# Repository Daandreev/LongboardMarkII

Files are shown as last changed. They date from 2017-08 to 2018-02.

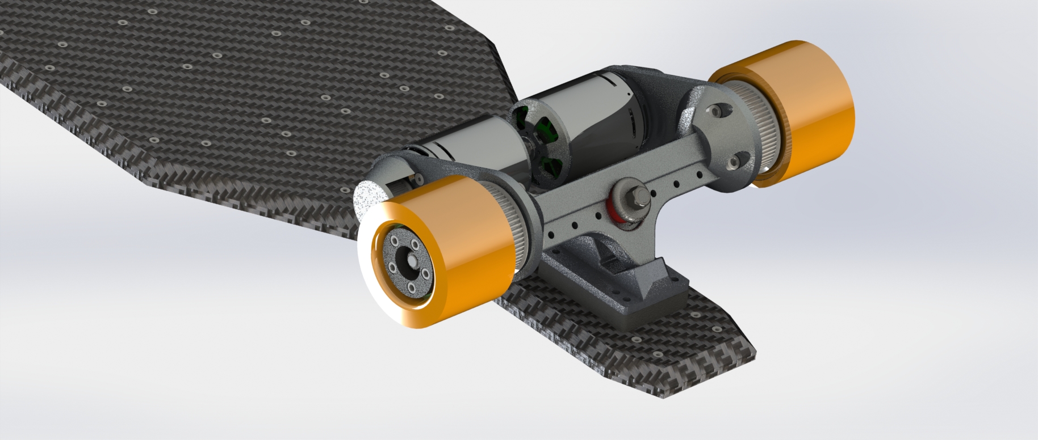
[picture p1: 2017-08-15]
CAD/MarkII/FullAssembly/Pictures/FullAssemblyImage1.JPG

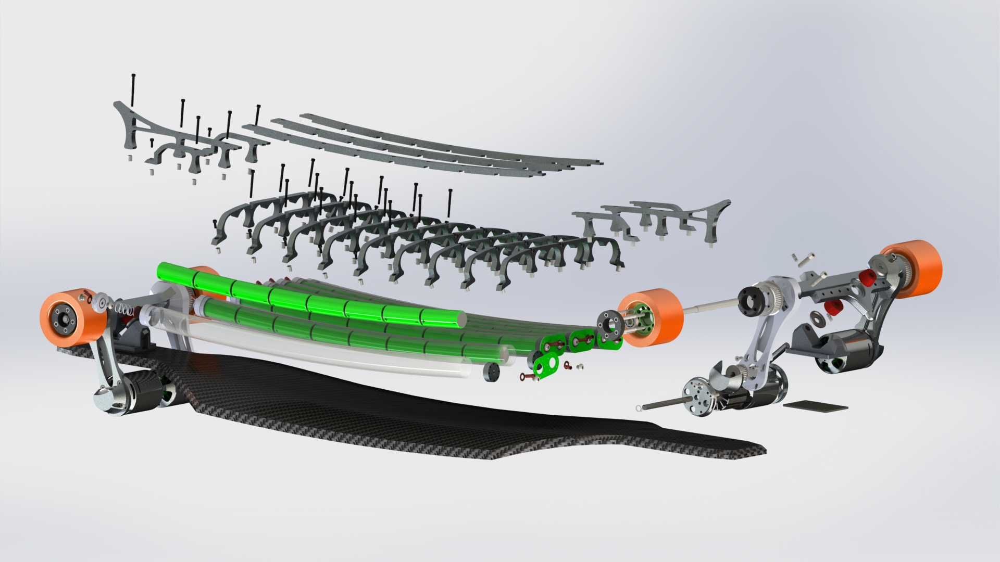
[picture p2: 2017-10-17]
Pictures/Full Assembly Exploded 2.JPG

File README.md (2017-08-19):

# LongboardMarkII

Ground up, over-engineered electric longboard

*****August 8, 2017*****

I want something under my ass that has enough potential energy packed into its batteries to fire a pound of bacon into the Asteroid Belt. 
Since nothing on the market fits the bill; I am building it myself.

With a sufficient disrespect for my own time and money I am learning every EE, ME, CS, Manufacturing technique necessary to complete aforementioned longboard.

The project started in my freshman year of college, Winter 2015.

[MarkI](https://www.instructables.com/id/Electric-Longboard-Mark-I/) was completed in the spring of 2016. It featured a whopping 35mph top speed, a pair of lead-acid scooter batteries giving it a theoretical range of about 4 miles of range, and a jaguaresque construction - requiring field-repairs every 2 miles.

MarkII was started soon after. Initially I focused on learning the electrical engineering skills necessary to create the Motor Drivers, BMS, and Headlights. 
	The Motor Drivers were my introduction to H-bridges and after creating a design that could vaguely spin a BLDC motor I opted out for [Vedder's VESC](http://vedder.se/2015/01/vesc-open-source-esc/)
	The BMS vas envisioned as an adaptive system that could be daisy chained across as many batteries as necessary, however that became more of a PCB design and manufacturing learning experience after I learned more about how they are made industrially.
	The headlights were and still are massively successful. With 5 watts of pure photon emission created by a triple bank of German OSRAM diodes, they are blindingly bright in all Red, Green, Blue and White colors. The issue is that I can’t run them on more than 10% brightness without facing serious heat management issues.
	
In parallel with the electronics, I created a few iterations of the deck. I constructed my own longboard-deck press by molding an initial foam model with cement. The initial few attempts at carbon fiber-foam composites failed, however on the 3rd iteration of the Baltic Birch - Carbon fiber Composite, I was able to produce a beautiful deck that stands at 48in tall and flexes less than an inch with 500lb on it.

I also learned how to use a few CAD packages, and CNC equipment to make the mounting hardware for the motors. Learning from the flimsy construction of the MarkI motor mounts I designed my own longboard trucks to accommodate the installation of a pair of 2250Watt motors. My designs were based on the Caliber II Longboard trucks.

As it stands, just about everything made in the past year needs to be reiterated.

My main focus now, is to involve more people. My friend Anton Zaytsev has been diligently helping me create a 1.5kW charger and another offered to do some of the software. However, I think this project can bring together a serious community interested in progressing high-tech DIY electrical vehicles.

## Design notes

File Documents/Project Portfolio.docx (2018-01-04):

Electric Longboard Mark II

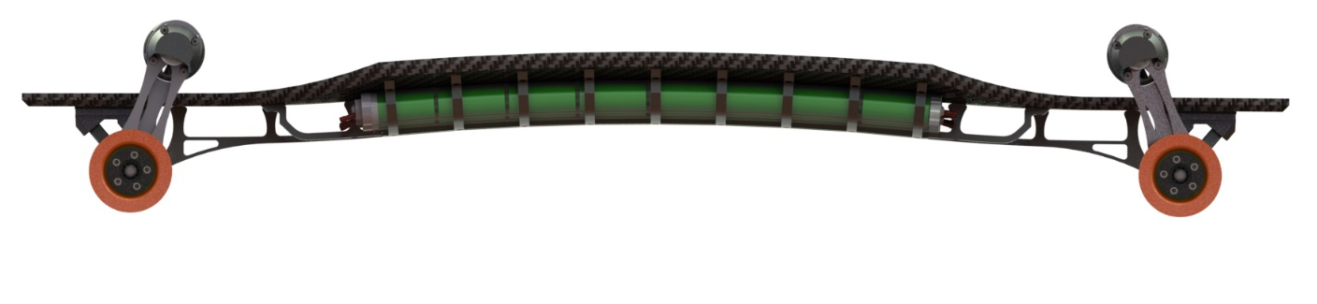
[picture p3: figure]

Open-Source Project by Daniil Andreev

Oct. 16, 2017

Motivation

The reasoning behind this project it is a natural progression of my interest in longboard and previous mechanics experience, as well as making a resume that I can literally ride to an interview. However, the initiating thought was; I want build something so outrageous it exists only in a Neal Stevenson universe.

The project started during the end of my first year as an undergrad at Knox College. I had looked at the commercially available Boosted Board and figured I could make something way more powerful.

Having no training in electronics, I spent the rest of the year attempting smaller projects that would help me build the skill required to attempt an electric vehicle. 3 years later I am just starting to see the finish line.

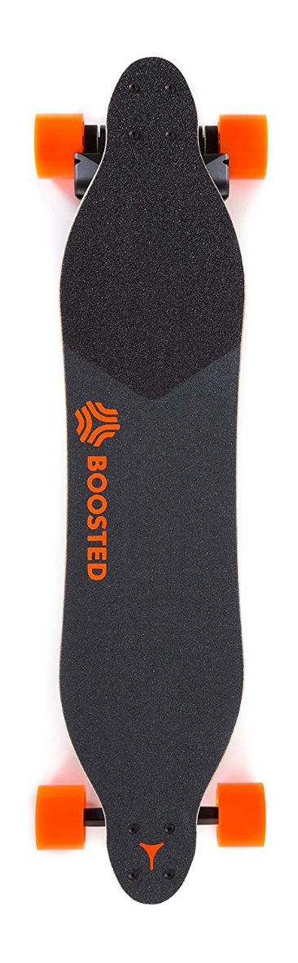
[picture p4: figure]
Image result for boosted
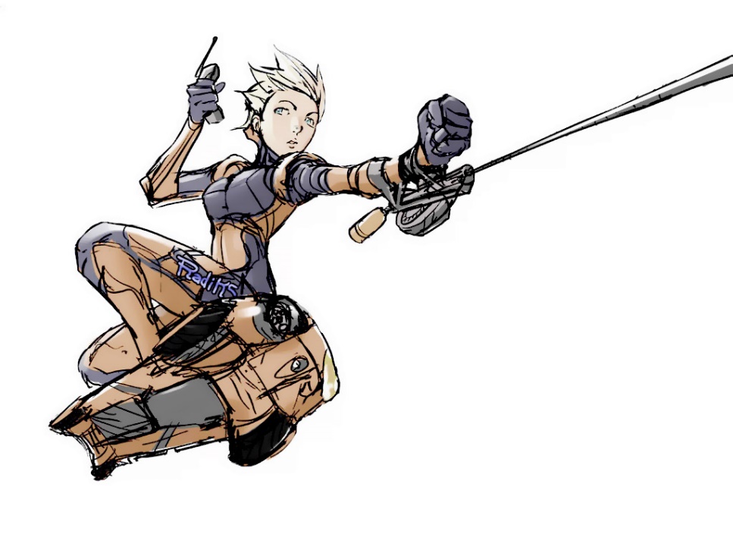
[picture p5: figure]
Image result for YT snow crash

Mechanical Design and Model

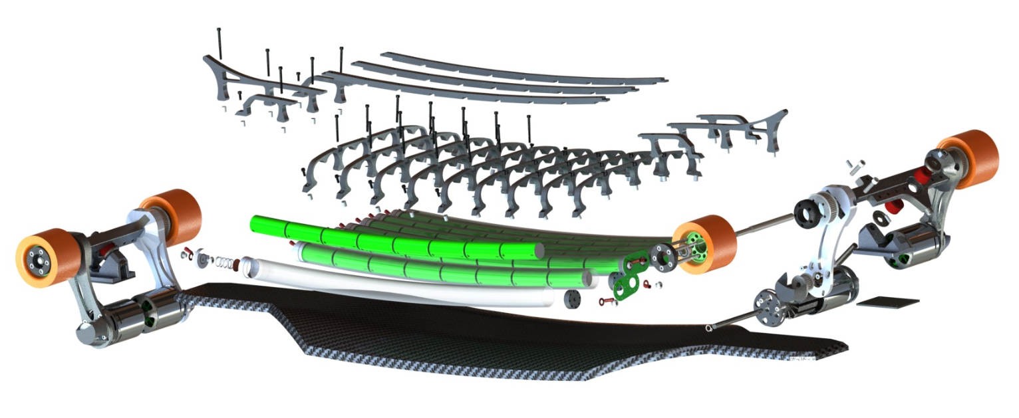
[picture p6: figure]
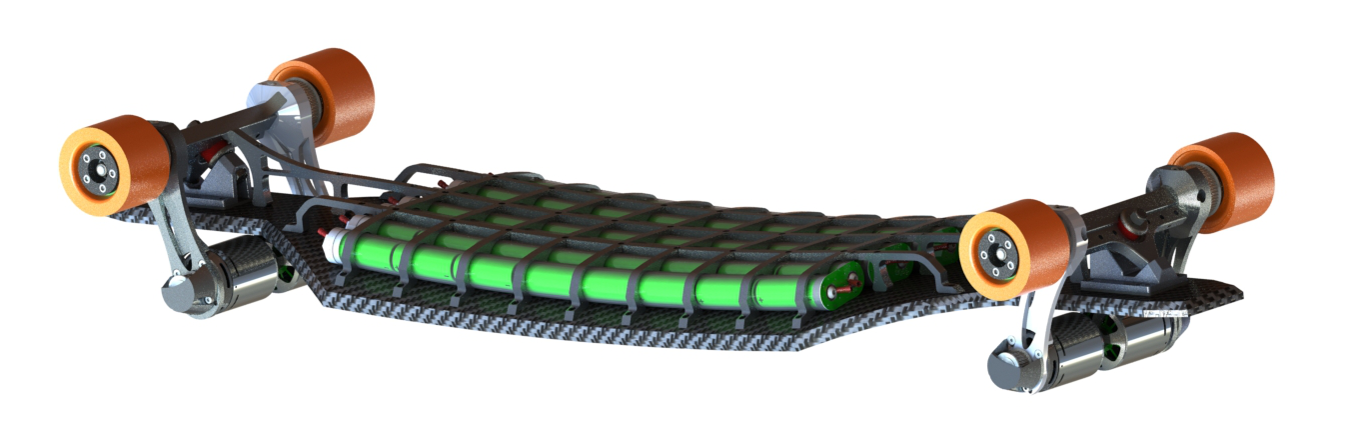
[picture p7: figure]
A close up of a device Description generated with very high confidence

After a year break in the building process I set out to reimagine the mechanical superstructure.

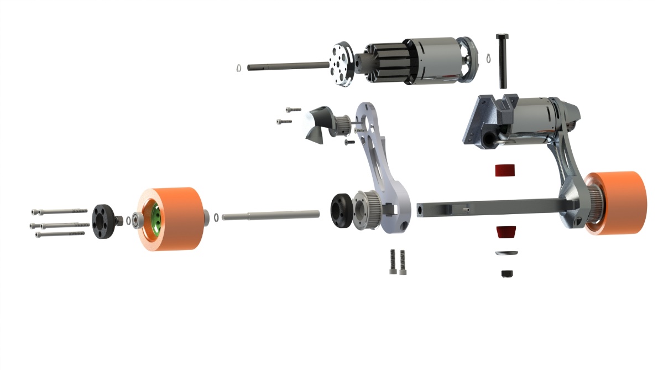
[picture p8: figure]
A close up of a device Description generated with high confidence

Completed

2015-2016

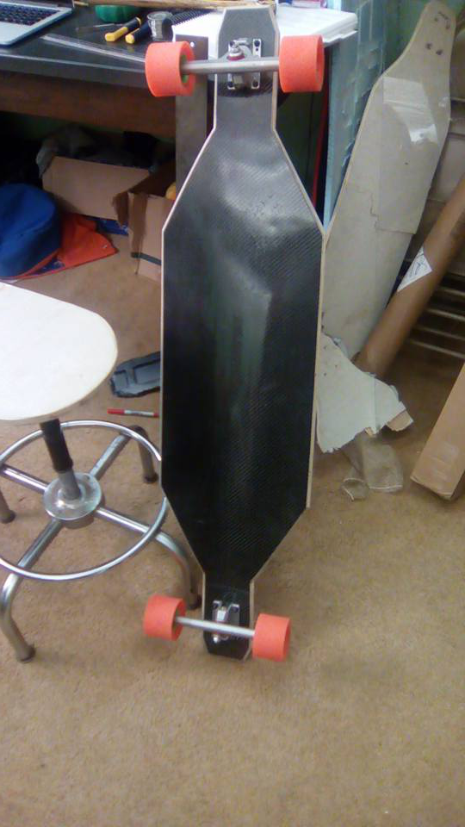
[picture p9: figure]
A picture containing indoor, floor, wall, table Description generated with very high confidence
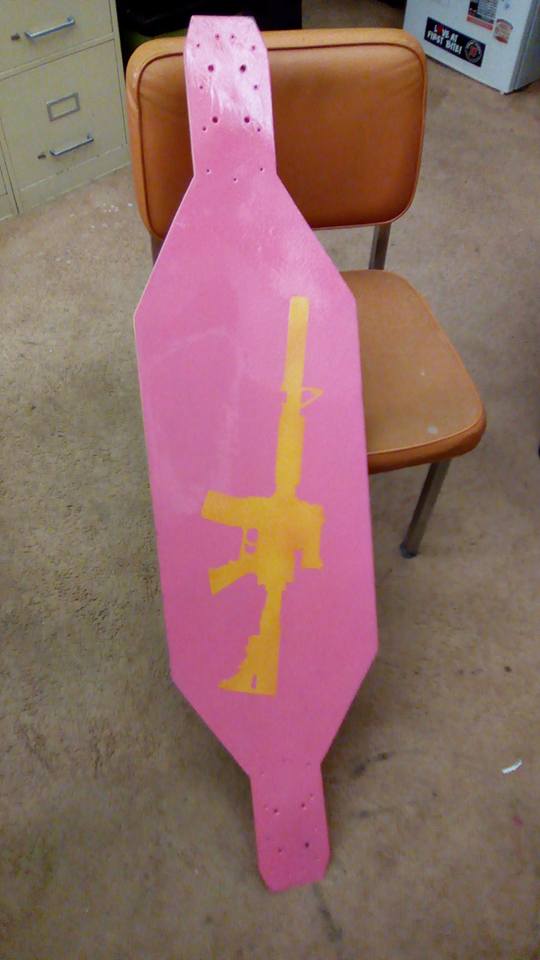
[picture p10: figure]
A sign on the floor Description generated with high confidence
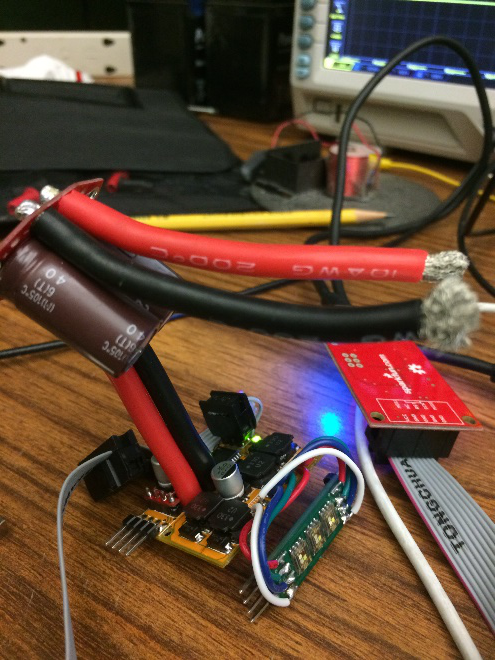
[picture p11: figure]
A picture containing floor, bicycle, indoor Description generated with very high confidence

V4 Carbon Fiber Deck | V2 10W RGBW Headlights, Backlights
3 failed designs | 4 x ILD6150 LED Drivers Atmel 328 Micro 12-65 operating voltage

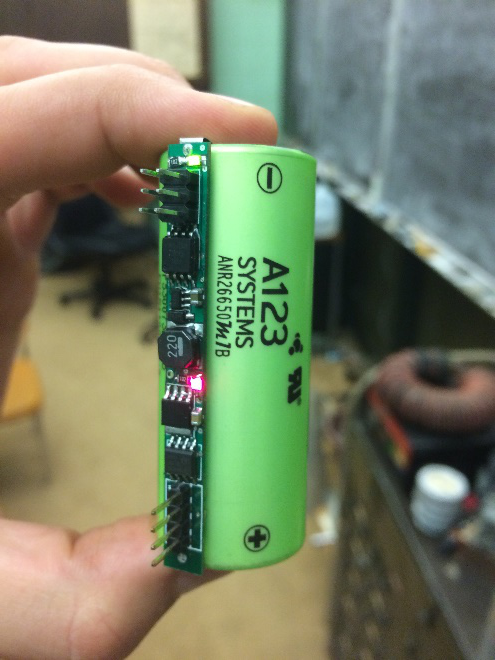
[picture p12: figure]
A circuit board Description generated with high confidence
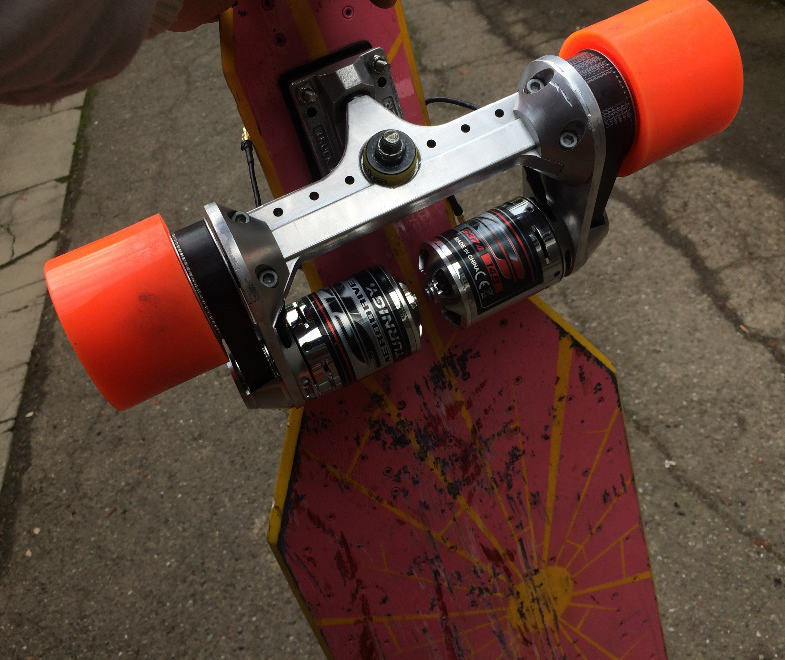
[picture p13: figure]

Daisy chainable single cell BMS | V1.5 Truck and Motor Assembly
Attiny 85 Micro Isolated I2C channel Onboard boost converter | 8kW Drive train 2 x Turnigy 7464 BLDC Motors 2 x Kegel Orangatang 80mm Wheels CNCed and turned at Redwood City Techshop.

In the Pipeline:

2017-

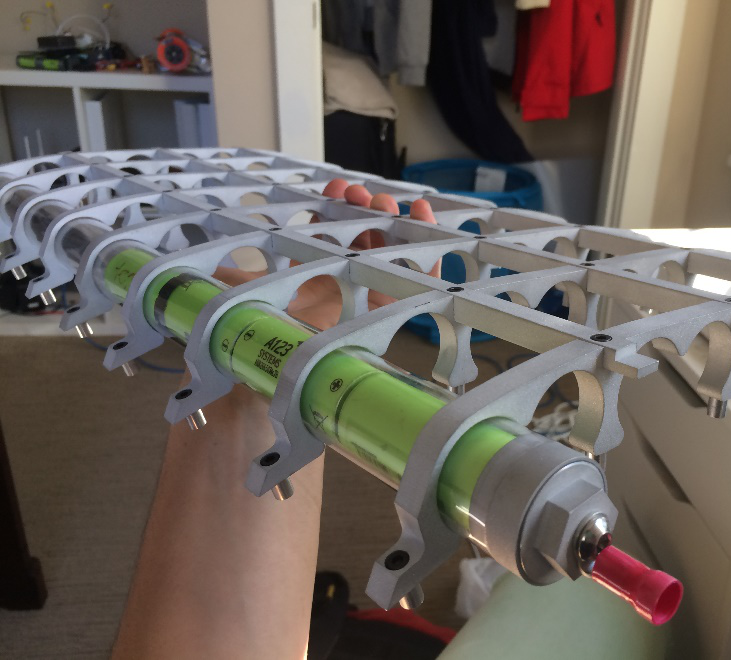
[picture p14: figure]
A picture containing indoor, wall, floor Description generated with very high confidence
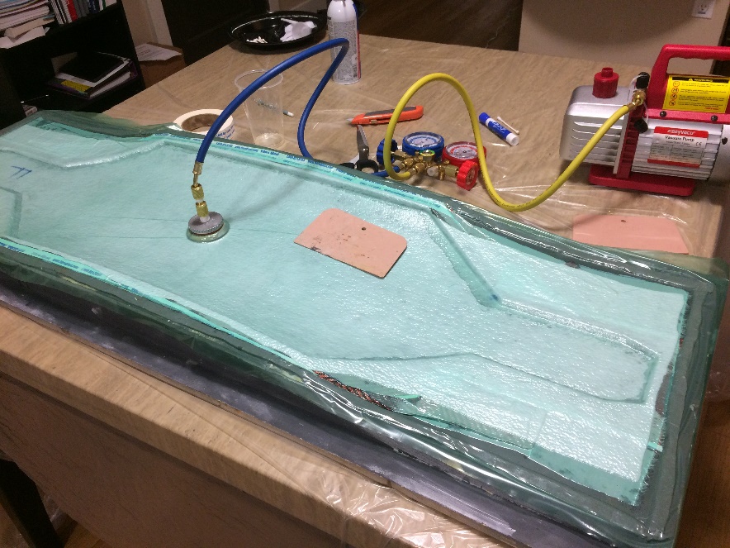
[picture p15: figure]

Battery Pack | Carbon fiber deck
64 LiFePO4 cells to deliver 200A @ 60V continuous | CNCed Molds Epoxy curing oven built.

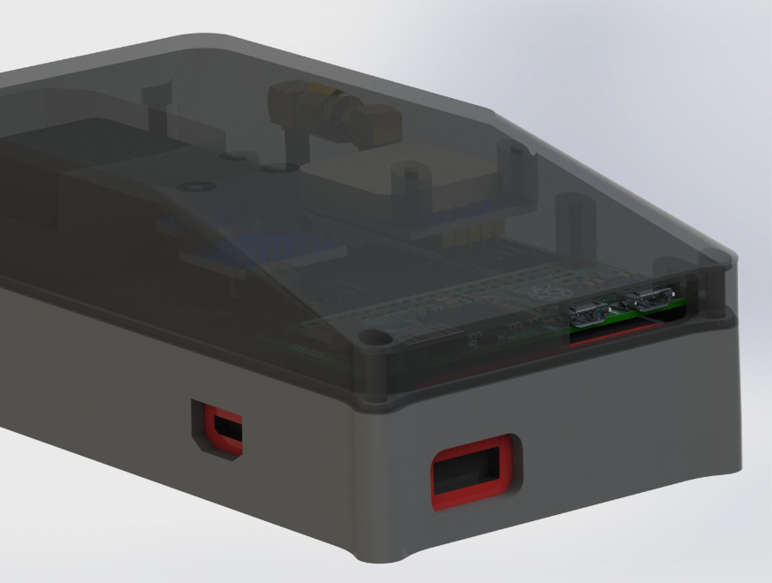
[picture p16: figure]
A picture containing sky, electronics Description generated with high confidence
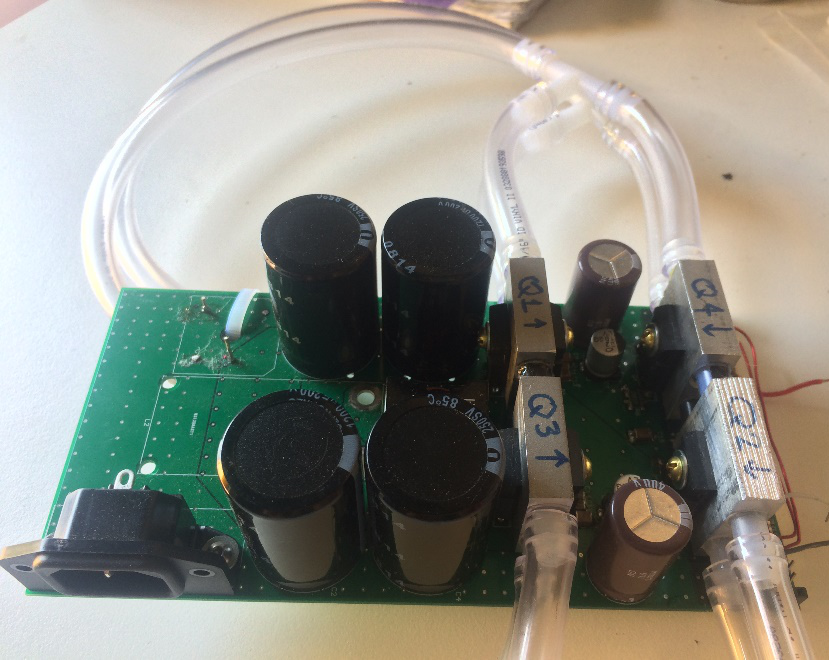
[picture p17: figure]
A picture containing table, indoor Description generated with very high confidence

Sensor Module | 1.5kW charger
Raspberry Pi central module GPS Altimeter Design and development in collaboration with Sam Ragsdale | Tested at 900W without water-cooling Compatible with 240V for 3kW+ charging Design and development in collaboration with Anton Zaytsev

In the Near Future

Headlight, Backlight enclosure

Integrated battery management system

Water-resistant cover

Remote-control system

2 x V2 trucks and motor mounts for the full 16kW drive train.

Learning Experience

This project helped me become a full stack developer. Having the opportunity to design and manufacture the whole project from scratch taught me to be very considerate of my design choices; making sure that the hardware is compatible with the electronics and software, striking the balance between aesthetic design and ease of manufacture. To make this board a reality I had to crawl along the entire industrial process, learning the properties of plastics, metals, composites and their respective postprocessing techniques. I learned to do the gritty work as well, to not only design and build, but talk to PCB manufacturers, spend hours on the phone with hardware suppliers, and read endless datasheets, weigh the properties of different chipsets and picking products that integrate with the full stack development process.

The top five skills that I this project taught me:

CAD – Solidworks, Eagle

Electronics – Circuit Design, PCB Design, Manufacture

C programming – Firmware development

Manufacturing – CNC, Lathe, Mill, Carbon Fiber Molding

Self-Teaching – The ability to research, learn and use any new skill or _ information that I need to push the project along

In Conclusion

Experiencing the width of the engineering process has inspired me to join a EE master program and join the hardware world to make products that have a physical impact.

Components not designed or manufacture by project team

VESC – BLDC motor speed controller

Turnigy 6374 BLDC motors

Nyko Wii nunchuck – repurposed for the control of the ESCs

Kegel Orangatang 80mm Wheels

More Info

Hackaday Project Page (https://hackaday.io/project/26899-electric-longboard-markii)

Github (https://github.com/lolomolo/LongboardMarkII)

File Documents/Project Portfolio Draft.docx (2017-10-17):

Electric Longboard Mark II


Open-Source Project by Daniil Andreev

Oct. 16, 2017

Contributors

| Anton Zaytzev | - Reed College
| Sam Ragsdale | - Washington University in St. Louis

Motivation

The reasoning behind this project is simply my interest in building stuff, as well as something akin to being able to ride my own resume to a job interview. But the initiating thought was; to build something so outrageous it would stink of Snowcrash.

The project started during the end of my first year as an undergrad at Knox College. I had looked at the commercially available Boosted Board and figured I could make something way more powerful.

Having no training in electronics, I spent the rest of the year attempting smaller projects that would help me build the skill required to attempt an electric vehicle. 3 years later and 12k in, I am just starting to see the finish line.

Image result for boosted
Image result for YT snow crash

Mechanical Design and Model

A close up of a device Description generated with very high confidence

After a year break in the building process I set out to reimagine the mechanical superstructure.

A close up of a device Description generated with high confidence

Completed

2014-2015

A picture containing indoor, floor, wall, table Description generated with very high confidence
A sign on the floor Description generated with high confidence
A picture containing floor, bicycle, indoor Description generated with very high confidence

V4 Carbon Fiber Deck | V2 10W RGBW Headlights, Backlights
3 failed designs | 4 x ILD6150 LED Drivers Atmel 328 Micro 12-65 operating voltage

A circuit board Description generated with high confidence

Daisy chainable single cell BMS | Custom Truck and Motor Assembly
Attiny 85 Micro Isolated I2C channel Onboard boost converter | 2 x Turnigy 7464 BLDC Motors 2 x Kegel Orangatang 80mm Wheels CNCed and turned at Redwood City Techshop.

In the Pipeline:

2017-

A picture containing indoor, wall, floor Description generated with very high confidence
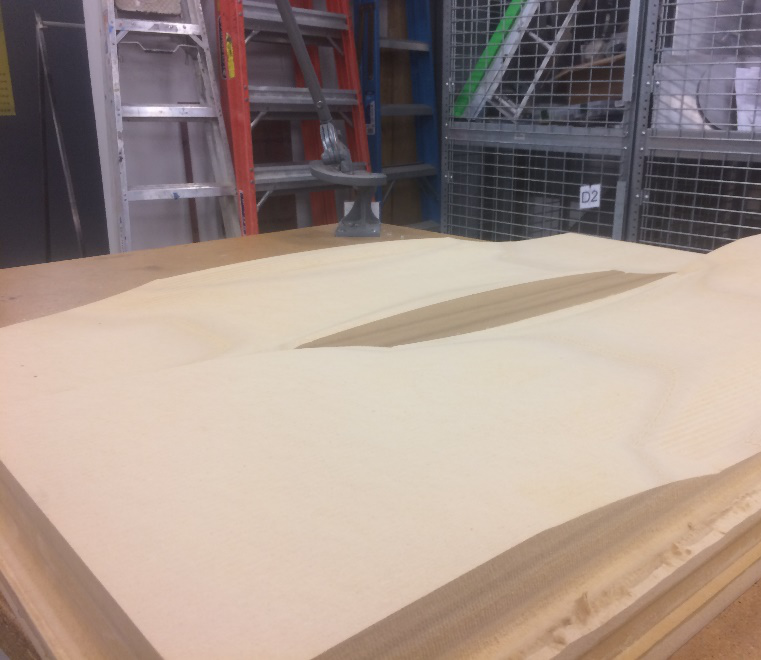
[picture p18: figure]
A picture containing indoor, window, table, building Description generated with high confidence

Battery Pack | Carbon fiber deck
Needs high current contacts in between the batteries as well as the wiring from the individual cells to the BMS | Molds CNCed Carbon fiber bought

A picture containing sky, electronics Description generated with high confidence
A picture containing table, indoor Description generated with very high confidence

Sensor Module | 1.5kW charger
Raspberry Pi central module GPS Altimeter Design and development in collaboration with Sam Ragsdale | Tested at 900W withought water-cooling Compatible with 240V for 3kW+ charging Design and development in collaboration with Anton Zaytsev

In the Near Future

Headlight, Backlight enclosure

Integrated battery management system

Waterproofing cover

Remote-control system

Components not designed or manufacture by project team:

VESC – BLDC motor speed controller

Turnigy 6374 BLDC motors

Nyko Wii nunchuck – repurposed for the control of the ESCs

Kegel Orangatang 80mm Wheels

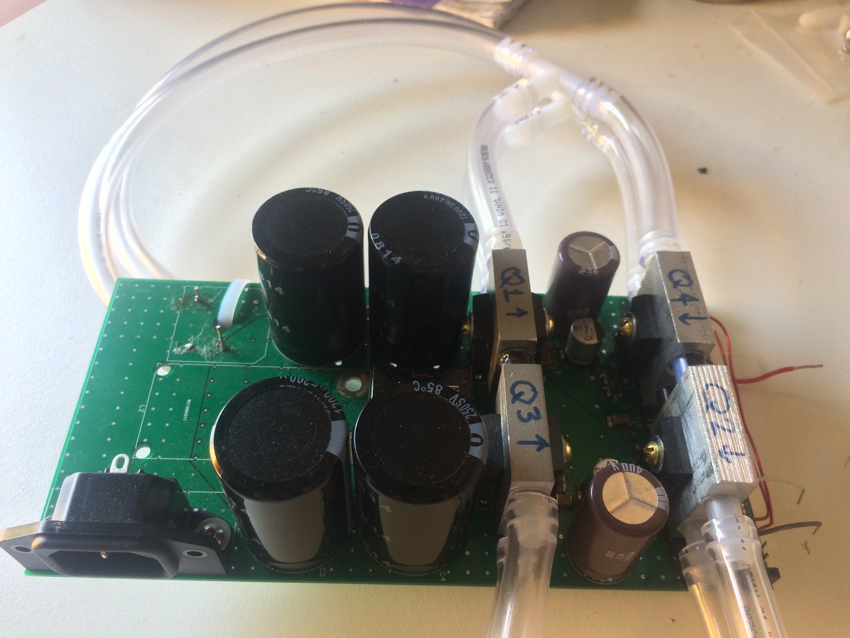
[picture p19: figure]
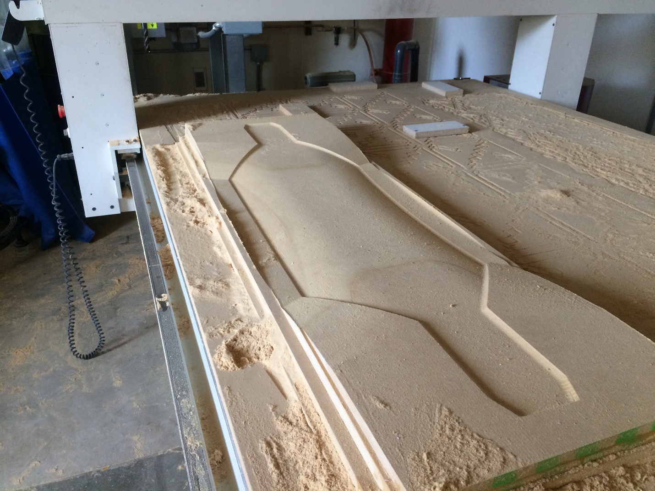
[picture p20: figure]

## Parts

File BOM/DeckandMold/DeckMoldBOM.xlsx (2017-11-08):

Mold | Item Name | Item obtained? | Item Location | Item Price | Quanitity | Quanity Units | Item Desc | Multiplyer | Tax | Shipping | Total | Sub Total | Grand Total | Purchase Total
 | MDF | Y | Home Depot | 26.99 | 5 | Sheet | .75" thick 48"x96" | 1 | 0.08 | 0 | 145.746 |  | 145.746 | 0
 | Wood Glue | Y | Home Depot | 6.98 | 2 |  |  | 1 | 0.08 | 0 | 15.0768 |  | 160.8228 | 0
 | Chisel Set | Y | https://www.amazon.com/VonHaus-Craftsman-Woodworking-Carving-Sharpening/dp/B014DT8KYG | 34.99 | 1 | set | for correcting mold | 1 | 0.08 | 0 | 37.7892 |  | 198.612 | 0
 | Wood Putty | Y | Home Depot | 10 | 1 | tub | for correcting mold | 1 | 0.08 | 0 | 10.8 |  | 209.412 | 0
 | Machining Costs | Y | Architecture School | 20 | 3 | 3 hours | to run the wood router | 1 | 0.08 | 0 | 64.8 |  | 274.212 | 0
 | Hex Bolt | Y | https://www.mcmaster.com/#91247a560/=1a608ny | 0.33 | 25 | bolts | 1/4"-20 4" clamp mold together | 1 | 0.08 | 0 | 8.91 |  | 283.122 | 0
 | Shaft | Y | https://www.mcmaster.com/#catalog/123/1129/=1a607rw | 9.87 | 1 | units | 3/16" x 18" align mold | 1 | 0.08 | 0 | 10.6596 |  | 293.7816 | 0
 | Tee Nut | Y | https://www.mcmaster.com/#90975a029/=1a608zr | 0.1024 | 100 | nuts | 1/4"-20 | 1 | 0.08 | 0 | 11.0592 |  | 304.8408 | 0
 | Ball Endmill 1/2" | Y | https://www.mcmaster.com/#8909a45/=1a609yk | 61.6 | 1 | endmill | 1/2"x5" ball end | 1 | 0.08 | 20 | 66.528 |  | 391.3688 | 0
 | Mold Primer | Y |  | 51.95 | 2 | Quart | Duratec Gray 1041-A | 0.9 | 0 | 9.95 | 93.51 |  | 494.8288
 | MEKP hardender | Y |  | 2.95 | 2 | oz | 69-A hardener | 0.9 | 0 | 0 | 5.31 |  | 500.1388
 | Step 1,2 Polish | Y |  | 16.15 | 2 | lb | 1102-A,1103-A | 0.9 | 0 | 19.95 | 29.07 |  | 549.1588
Vaccuming | Item Name | Item obtained? | Item Location | Item Price | Quanitity | Quanity Units | Item Desc | Multiplyer | Tax | Shipping | Total | Sub Total | Grand Total | Purchase Total
 | 581-A Sealant Tape | Y | http://www.fibreglast.com/product/gray-sealant-tape-00581/Vacuum_Bagging_Films_Peel_Ply_Tapes | 10.95 | 1 | roll | 25' | 1 | 0.08 | 0 | 11.826 |  | 11.826 | 0
 | 1678-C Stretchlon | Y | http://www.fibreglast.com/product/stretchlon-200-bagging-film-1678/Vacuum_Bagging_Films_Peel_Ply_Tapes | 3.99 | 5 | Yards | Bagging Film 60" Width | 1 | 0.08 | 0 | 21.546 |  | 33.372 | 0
 | 582-B Peel Ply | Y | http://www.fibreglast.com/product/Nylon_Released_Peel_Ply_582/Vacuum_Bagging_Films_Peel_Ply_Tapes | 13.31666667 | 3 | Yards | 60" Width | 1 | 0.08 | 0 | 43.146 |  | 76.518 | 0
 | 1779-C BreatherCloth | Y | http://www.fibreglast.com/product/Breather_and_Bleeder_579/Vacuum_Bagging_Films_Peel_Ply_Tapes | 7.99 | 5 | Yards | 60" Width 7oz | 1 | 0.08 | 0 | 43.146 |  | 119.664 | 0
 | 1153 FibRelease | Y | http://www.fibreglast.com/product/FibRelease_01153_A/Mold_Releases | 26.95 | 1 | 32 Oz. | Release agent for the mold | 1 | 0.08 | 0 | 29.106 |  | 148.77 | 0
 | 1735-A Line Tape | Y | http://www.fibreglast.com/product/perfect-line-tape-01735/Tapes | 14.95 | 1 | Roll | 55 Yards | 1 | 0.08 | 0 | 16.146 |  | 164.916 | 0
 | 118-A Mold polish and release wax | Y |  | 21.95 | 1 | Tin | 11oz | 1 | 0.08 | 0 | 23.706 |  | 188.622
CarbonV2 | Item Name | Item obtained? | Item Location | Item Price | Quanitity | Quanity Units | Item Desc | Multiplyer | Tax | Shipping | Total | Sub Total | Grand Total | Purchase Total
 | CarbonKevlar Orange | Y | https://www.rockwestcomposites.com/materials-tools/fabrics-pre-pregs-tow/carbon-kevlar-hybrid-fabric/13010-orange-d | 52.79 | 2 | Yards | .009" thick 50" Width 2x2 twill | 1 | 0.08 | 13.6 | 114.0264 |  | 127.6264 | 0
 | 1072-C Carbon 12K weave | Y | http://www.fibreglast.com/product/1072_12K_Carbon/carbon-fiber-fabric-classic-styles | 73.99 | 5 | Yards | .03" thick 50" Width | 0.8 | 0.08 | 0 | 319.6368 |  | 447.2632 | 0
 | 2000-B System 2000 Epoxy Resin | Y | http://www.fibreglast.com/product/System_2000_Epoxy_Resin_2000/Epoxy_Resins | 104.95 | 1 | Gallon |  | 0.8 | 0.08 | 0 | 90.6768 |  | 537.94 | 0
 | 2120-B System 2000 Epoxy Hardener | Y | http://www.fibreglast.com/product/System_2000_Epoxy_Resin_2000/Epoxy_Resins | 44.95 | 1 | Quart | 120min pot life | 0.8 | 0.08 | 0 | 38.8368 |  | 576.7768 | 0
 | 1022-A Vinyl Foam | Y |  | 31.95 | 2 | Sheet | 32"*48" 1/8Thickness | 0.8 | 0.08 | 0 | 55.2096 |  | 631.9864 | 0 | 1545.834
 | 2543-C FiberGlass | Y |  | 12.99 | 5 | yards | 7781 E-glass | 0.8 | 0.08 | 119.95 | 56.1168 |  | 808.0532 | 0

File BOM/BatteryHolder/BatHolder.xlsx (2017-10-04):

 | Item Name | Item obtained? | Item Location | Item Price | Quanitity | Quanity Units | Item Desc | Multiplyer | Tax | Shipping | Total | Grand Total | Purchase Total
 | 6'x3 1/2"x3/8" Aluminum | Y | https://www.mcmaster.com/#8975k617/=19bnny9 | 7.875 | 6 | feet |  | 1 | 0.08 | 0 | 51.03 | 51.03 | 0
 | 6'x3/8"x3/8" Aluminum | Y | https://www.mcmaster.com/#9008k78/=19bno32 | 1.135 | 6 | feet |  | 1 | 0.08 | 33 | 7.3548 | 91.3848 | 0
 | 6'x3"x3/8" Aluminum | Y | https://www.mcmaster.com/#8975k91/=19evlb8 | 9.385 | 2 | feet |  | 1 | 0.08 | 33 | 20.2716 | 144.6564 | 0
 | Aluminum spacers 5/16" | Y | https://www.mcmaster.com/#9008k78/=19bno32 | 0.28 | 75 | units | 6-32 thread | 1 | 0.08 | 0 | 22.68 | 167.3364 | 0
 | Black Oxide Screw 1.50" | Y | https://www.mcmaster.com/#91251a157/=19evjrx | 0.1988 | 50 | units | 6-32 thread | 1 | 0.08 | 0 | 10.7352 | 178.0716 | 0
 | polycarbonate tube | Y | https://www.mcmaster.com/#8585k205/=19bof2z | 2.48625 | 16 | feet | 1.125" ID 1.25" OD | 1 | 0.08 | 0 | 42.9624 | 221.034 | 0
 | aluminum tube 1.25"OD | Y | https://www.mcmaster.com/#9056k76/=19bq239 | 12.1 | 1 | feet | 1.12"ID | 1 | 0.08 | 0 | 13.068 | 234.102 | 0
 | aluminum rod 1.25"OD | Y | https://www.mcmaster.com/#8974k16/=19bq4f4 | 10.54 | 2 | feet |  | 1 | 0.08 | 0 | 22.7664 | 256.8684 | 0
 | compression spring | Y | https://www.mcmaster.com/#9657k314/=19bqcva | 0.8625 | 12 | units | 1"Long .49"ID | 1 | 0.08 | 0 | 11.178 | 268.0464 | 0
 | Black Oxide Screw .375" | Y | https://www.mcmaster.com/#91251a146/=19bqn03 | 0.0842 | 100 | units | 6-32 thread | 1 | 0.08 | 0 | 9.0936 | 277.14 | 0
 | Black Oxide Screw 1.75" | Y | https://www.mcmaster.com/#91251a158/=19n12mv | 0.142 | 50 | UNITS | 6-32 thread | 1 | 0.08 | 0 | 7.668 | 284.808 | 0
 |  |  |  |  |  |  |  |  |  |  |  | 284.808 | 0
Electrical Connects |  |  |  |  |  |  |  | 1 |  |  | 0 | 284.808 | 0
 | copper disk 3/4" | Y | https://www.etsy.com/listing/62082177/copper-discs-20-gauge-stamping-blanks | 0.4 | 80 | units | 20 guage | 1 | 0.08 | 4.7 | 34.56 | 324.068 | 0
 | copper braid | Y | https://www.amazon.com/dp/B003HGHQVU/ref=biss_dp_t_asn | 20.01 | 1 | roll | 25'x.25" | 1 | 0.08 | 0 | 21.6108 | 345.6788 | 0
 | Ring Terminal | Y | https://www.mcmaster.com/#7113k444/=19bqfh1 | 0.5168 | 25 | units | .25"IDx.49"OD | 1 | 0.08 | 0 | 13.9536 | 359.6324 | 0
 | Copper Terminal screw .25" | Y | https://www.mcmaster.com/#92949a832/=19bqg8g | 0.1406 | 50 | units | 1/4"-20, 1/4"length | 1 | 0.08 | 0 | 7.5924 | 367.2248 | 0
 | Copper Bar | N | https://www.mcmaster.com/#8966k15/=19brdi6 | 6.596666667 | 0 | inches | 1.125"OD | 1 | 0.08 | 0 | 0 | 367.2248 | 0
 | Magnet wire 18 AWG | Y | https://www.amazon.com/Remington-Industries-18SNSP-Enameled-Diameter/dp/B00BJMVK02 | 0.08323383085 | 201 | feet | 18AWG | 1 | 0.08 | 0 | 18.0684 | 385.2932 | 0
Tooling |  |  |  |  |  |  |  |  |  |  |  | 385.2932 | 0
 | drill bit 9/64" | Y | https://www.mcmaster.com/#2901a116/=19brqzs | 1.67 | 4 | unit | 9/64" 1.53" cut depth | 1 | 0.08 | 0 | 7.2144 | 392.5076 | 0
 | Ball Endmill 3/4" | Y | https://www.mcmaster.com/#2866a84/=19n16ap | 109.68 | 1 | unit | 4" length of cut | 1 | 0.08 | 0 | 118.4544 | 510.962 | 0
 | drill bit 3/16" | Y | https://www.mcmaster.com/#87755a29/=19n185a | 2.21 | 3 | units | 1.75" length of cut | 1 | 0.08 | 0 | 7.1604 | 518.1224 | 0
 | Mold Machining work | Y |  | 20 | 3 | hours | machining work on mold at architecture school | 1 | 0 | 1.5 | 60 | 579.6224 | 0
 | Tap 1_3/16" 16TPI | Y | http://www.ebay.com/itm/112386053946 | 28.99 | 1 | unit |  | 1 | 0 | 0 | 28.99 | 608.6124 | 0
 | Die 1_3/16" 16TPI | Y | http://www.ebay.com/itm/181930002652 | 27 | 1 | unit |  | 1 | 0 | 0 | 27 | 635.6124 | 0

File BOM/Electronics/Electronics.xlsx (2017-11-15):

Mold | Item Name | Item obtained? | Item Location | Item Price | Quanitity | Quanity Units | Item Desc | Multiplyer | Tax | Shipping | Total | Sub Total | Grand Total | Purchase Total
 | Vesc | Y |  | 100 | 2 |  |  | 1 | 0.08 | 0 | 216 |  | 216 | 0
 | Turnigy Motor | Y |  | 80 | 2 |  |  | 1 | 0.08 | 0 | 172.8 |  | 388.8 | 0
 | Batteries | Y |  | 10 | 64 |  |  | 1 | 0.08 | 0 | 691.2 |  | 1080 | 0

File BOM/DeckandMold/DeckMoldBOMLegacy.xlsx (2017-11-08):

Mold | Item Name | Item obtained? | Item Location | Item Price | Quanitity | Quanity Units | Item Desc | Multiplyer | Tax | Shipping | Total | Sub Total | Grand Total | Purchase Total
 | MDF | Y | Home Depot | 26.99 | 5 | Sheet | .75" thick 48"x96" | 1 | 0.08 | 0 | 145.746 |  | 145.746 | 0
 | Wood Glue | Y | Home Depot | 6.98 | 2 |  |  | 1 | 0.08 | 0 | 15.0768 |  | 160.8228 | 0
 | Chisel Set | Y | https://www.amazon.com/VonHaus-Craftsman-Woodworking-Carving-Sharpening/dp/B014DT8KYG | 34.99 | 1 | set | for correcting mold | 1 | 0.08 | 0 | 37.7892 |  | 198.612 | 0
 | Wood Putty | Y | Home Depot | 10 | 1 | tub | for correcting mold | 1 | 0.08 | 0 | 10.8 |  | 209.412 | 0
 | Machining Costs | Y | Architecture School | 20 | 3 | 3 hours | to run the wood router | 1 | 0.08 | 0 | 64.8 |  | 274.212 | 0
 | Hex Bolt | Y | https://www.mcmaster.com/#91247a560/=1a608ny | 0.33 | 25 | bolts | 1/4"-20 4" clamp mold together | 1 | 0.08 | 0 | 8.91 |  | 283.122 | 0
 | Shaft | Y | https://www.mcmaster.com/#catalog/123/1129/=1a607rw | 9.87 | 1 | units | 3/16" x 18" align mold | 1 | 0.08 | 0 | 10.6596 |  | 293.7816 | 0
 | Tee Nut | Y | https://www.mcmaster.com/#90975a029/=1a608zr | 0.1024 | 100 | nuts | 1/4"-20 | 1 | 0.08 | 0 | 11.0592 |  | 304.8408 | 0
 | Ball Endmill 1/2" | Y | https://www.mcmaster.com/#8909a45/=1a609yk | 61.6 | 1 | endmill | 1/2"x5" ball end | 1 | 0.08 | 20 | 66.528 |  | 391.3688 | 0
 | Mold Primer | Y |  | 51.95 | 2 | Quart | Duratec Gray 1041-A | 0.9 | 0 | 9.95 | 93.51 |  | 494.8288
 | MEKP hardender | Y |  | 2.95 | 2 | oz | 69-A hardener | 0.9 | 0 | 0 | 5.31 |  | 500.1388
 | Step 1,2 Polish | Y |  | 16.15 | 2 | lb | 1102-A,1103-A | 0.9 | 0 | 19.95 | 29.07 |  | 549.1588
Vaccuming | Item Name | Item obtained? | Item Location | Item Price | Quanitity | Quanity Units | Item Desc | Multiplyer | Tax | Shipping | Total | Sub Total | Grand Total | Purchase Total
 | 581-A Sealant Tape | Y | http://www.fibreglast.com/product/gray-sealant-tape-00581/Vacuum_Bagging_Films_Peel_Ply_Tapes | 10.95 | 1 | roll | 25' | 1 | 0.08 | 0 | 11.826 |  | 11.826 | 0
 | 1678-C Stretchlon | Y | http://www.fibreglast.com/product/stretchlon-200-bagging-film-1678/Vacuum_Bagging_Films_Peel_Ply_Tapes | 3.99 | 5 | Yards | Bagging Film 60" Width | 1 | 0.08 | 0 | 21.546 |  | 33.372 | 0
 | 582-B Peel Ply | Y | http://www.fibreglast.com/product/Nylon_Released_Peel_Ply_582/Vacuum_Bagging_Films_Peel_Ply_Tapes | 13.31666667 | 3 | Yards | 60" Width | 1 | 0.08 | 0 | 43.146 |  | 76.518 | 0
 | 1779-C BreatherCloth | Y | http://www.fibreglast.com/product/Breather_and_Bleeder_579/Vacuum_Bagging_Films_Peel_Ply_Tapes | 7.99 | 5 | Yards | 60" Width 7oz | 1 | 0.08 | 0 | 43.146 |  | 119.664 | 0
 | 1153 FibRelease | Y | http://www.fibreglast.com/product/FibRelease_01153_A/Mold_Releases | 26.95 | 1 | 32 Oz. | Release agent for the mold | 1 | 0.08 | 0 | 29.106 |  | 148.77 | 0
 | 1735-A Line Tape | Y | http://www.fibreglast.com/product/perfect-line-tape-01735/Tapes | 14.95 | 1 | Roll | 55 Yards | 1 | 0.08 | 0 | 16.146 |  | 164.916 | 0
 | 118-A Mold polish and release wax | Y |  | 21.95 | 1 | Tin | 11oz | 1 | 0.08 | 0 | 23.706 |  | 188.622
CarbonV2 | Item Name | Item obtained? | Item Location | Item Price | Quanitity | Quanity Units | Item Desc | Multiplyer | Tax | Shipping | Total | Sub Total | Grand Total | Purchase Total
 | CarbonKevlar Orange | Y | https://www.rockwestcomposites.com/materials-tools/fabrics-pre-pregs-tow/carbon-kevlar-hybrid-fabric/13010-orange-d | 52.79 | 2 | Yards | .009" thick 50" Width 2x2 twill | 1 | 0.08 | 13.6 | 114.0264 |  | 127.6264 | 0
 | 1072-C Carbon 12K weave | Y | http://www.fibreglast.com/product/1072_12K_Carbon/carbon-fiber-fabric-classic-styles | 73.99 | 5 | Yards | .03" thick 50" Width | 0.8 | 0.08 | 0 | 319.6368 |  | 447.2632 | 0
 | 2000-B System 2000 Epoxy Resin | Y | http://www.fibreglast.com/product/System_2000_Epoxy_Resin_2000/Epoxy_Resins | 104.95 | 1 | Gallon |  | 0.8 | 0.08 | 0 | 90.6768 |  | 537.94 | 0
 | 2120-B System 2000 Epoxy Hardener | Y | http://www.fibreglast.com/product/System_2000_Epoxy_Resin_2000/Epoxy_Resins | 44.95 | 1 | Quart | 120min pot life | 0.8 | 0.08 | 0 | 38.8368 |  | 576.7768 | 0
 | 1022-A Vinyl Foam | Y |  | 31.95 | 2 | Sheet | 32"*48" 1/8Thickness | 0.8 | 0.08 | 0 | 55.2096 |  | 631.9864 | 0 | 1545.834
 | 2543-C FiberGlass | Y |  | 12.99 | 5 | yards | 7781 E-glass | 0.8 | 0.08 | 119.95 | 56.1168 |  | 808.0532 | 0
"------------LEGACY-------------------"
All Carbon | Item Name | Item obtained? | Item Location | Item Price | Quanitity | Quanity Units | Item Desc | Multiplyer | Tax | Shipping | Total | Sub Total | Grand Total | Purchase Total
 | CarbonKevlar | N | http://www.fibreglast.com/product/kevlar-carbon-hybrid-yellow-1065/carbon-kevlar-hybrid-fabric | 69.95 | 1 | Yards | .012" thick 50" Width | 1 | 0.08 | 0 | 75.546 |  | 75.546 | 75.546
 | Carbon 6K weave | N | http://www.fibreglast.com/product/1073_6K_Carbon/carbon-fiber-fabric-classic-styles | 65.99 | 5 | Yards | .017" thick 50" Width | 1 | 0.08 | 0 | 356.346 |  | 356.346 | 431.892
 | System 2000 Epoxy Resin | N | http://www.fibreglast.com/product/System_2000_Epoxy_Resin_2000/Epoxy_Resins | 104.95 | 1 | Gallon |  | 1 | 0.08 | 0 | 113.346 |  | 113.346 | 545.238
 | System 2000 Epoxy Hardener | N | http://www.fibreglast.com/product/System_2000_Epoxy_Resin_2000/Epoxy_Resins | 44.95 | 1 | Quart | 120min pot life | 1 | 0.08 | 0 | 48.546 |  | 48.546 | 593.784
 | Polystyrene 5/32" | N | https://www.mcmaster.com/#8734k26/=197ppcb | 64.48 | 1 | Sheet | 72"*40" 5/32Thickness | 1 | 0.08 | 0 | 69.6384 |  | 69.6384 | 663.4224 | 663.4224
All FiberGlass | Item Name | Item obtained? | Item Location | Item Price | Quanitity | Quanity Units | Item Desc | Multiplyer | Tax | Shipping | Total | Sub Total | Grand Total | Purchase Total
 | FiberGlass | N | http://www.fibreglast.com/product/Style_7781_E_Glass_543/Fiberglass_Fabric | 12.09 | 5 | Yards | style 7781 E glass | 1 | 0.08 | 0 | 65.286 |  | 65.286 | 65.286
 | System 2000 Epoxy Resin | N | http://www.fibreglast.com/product/System_2000_Epoxy_Resin_2000/Epoxy_Resins | 104.95 | 1 | Gallon |  | 1 | 0.08 | 0 | 113.346 |  | 113.346 | 178.632
 | System 2000 Epoxy Hardener | N | http://www.fibreglast.com/product/System_2000_Epoxy_Resin_2000/Epoxy_Resins | 44.95 | 1 | Quart | 120min pot life | 1 | 0.08 | 0 | 48.546 |  | 48.546 | 227.178
 | Polystyrene 5/32" | N | https://www.mcmaster.com/#8734k26/=197ppcb | 64.48 | 1 | Sheet | 72"*40" 5/32Thickness | 1 | 0.08 | 0 | 69.6384 |  | 69.6384 | 296.8164 | 296.8164
 |  |  |  |  |  |  |  |  |  |  | *** squeegy | breathing mask
 |  |  |  |  |  |  |  |  |  |  | **buckets
 |  |  |  |  |  |  |  |  |  |  | Cleaning Material
 |  |  |  |  |  |  |  |  |  |  | https://www.fiberglasshawaii.com/
FiberGlass | Item Name | Item obtained? | Item Location | Item Price | Quanitity | Quanity Units | Item Desc | Multiplyer | Tax | Shipping | Total |  | Grand Total | Purchase Total
 | Fiberglass | N | http://www.fibreglast.com/product/Style_7781_E_Glass_543/Fiberglass_Fabric | 12.09 | 5 | Yards |  | 1 | 0.08 | 0 | 65.286 |  | 65.286 | 65.286
 | System 2000 Epoxy Resin | N | http://www.fibreglast.com/product/System_2000_Epoxy_Resin_2000/Epoxy_Resins | 104.95 | 1 | Gallon |  | 1 | 0.08 | 0 | 113.346 |  | 178.632 | 178.632
 | System 2000 Epoxy Hardener | N | http://www.fibreglast.com/product/System_2000_Epoxy_Resin_2000/Epoxy_Resins | 44.95 | 1 | Quart | 120min pot life | 1 | 0.08 | 0 | 48.546 | 227.178 | 227.178 | 227.178
 | Polystyrene 3/32" | N | https://www.mcmaster.com/#8734k24/=1997idd | 40.74 | 1 | Sheet | 72"*40" 3/32Thickness | 1 | 0.08 | 0 | 43.9992 | 232.6212 | #REF! | #REF!
 | Sealant Tape | N | http://www.fibreglast.com/product/gray-sealant-tape-00581/Vacuum_Bagging_Films_Peel_Ply_Tapes | 10.95 | 1 | roll | 25' | 1 | 0.08 | 0 | 11.826 |  | #REF! | #REF!
 | Stretchlon | N | http://www.fibreglast.com/product/stretchlon-200-bagging-film-1678/Vacuum_Bagging_Films_Peel_Ply_Tapes | 3.99 | 5 | Yards | Bagging Film 60" Width | 1 | 0.08 | 0 | 21.546 |  | #REF! | #REF!
 | Peel Ply | N | http://www.fibreglast.com/product/Nylon_Released_Peel_Ply_582/Vacuum_Bagging_Films_Peel_Ply_Tapes | 13.31666667 | 3 | Yards | 60" Width | 1 | 0.08 | 0 | 43.146 |  | #REF! | #REF!
 | BreatherCloth | N | http://www.fibreglast.com/product/Breather_and_Bleeder_579/Vacuum_Bagging_Films_Peel_Ply_Tapes | 5.65 | 3 | Yards | 60" Width | 1 | 0.08 | 0 | 18.306 |  | #REF! | #REF!
 | FibRelease | N | http://www.fibreglast.com/product/FibRelease_01153_A/Mold_Releases | 26.95 | 1 | 32 Oz. | Release agent for the mold | 1 | 0.08 | 0 | 29.106 |  | #REF! | #REF!
 | Line Tape | N | http://www.fibreglast.com/product/perfect-line-tape-01735/Tapes | 14.95 | 1 | Roll | 55 Yards | 1 | 0.08 | 0 | 16.146 |  | #REF! | #REF!

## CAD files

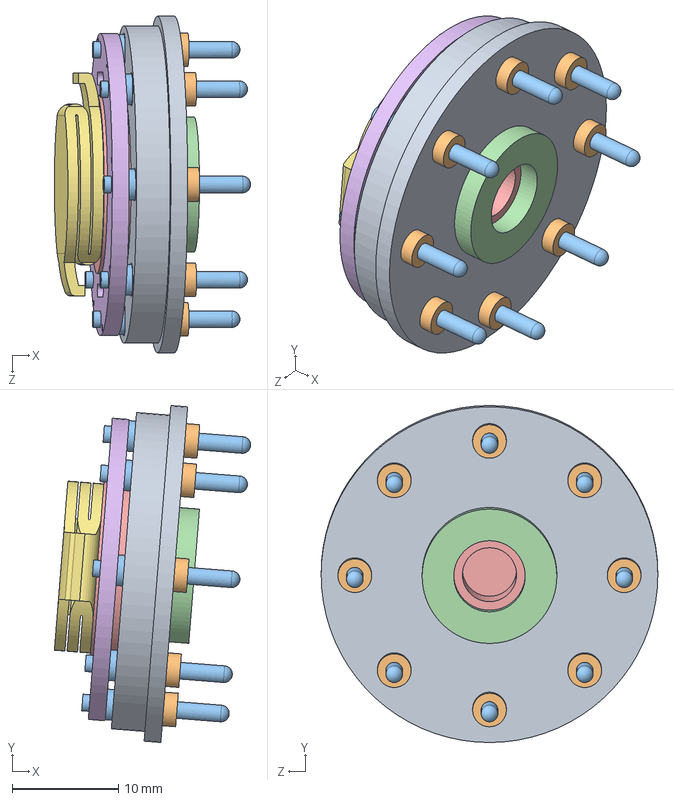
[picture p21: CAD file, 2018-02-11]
CAD/MarkII/BatteryPack/EndCap8Pin-Plastic.SLDASM
18.5 x 31.8 x 31.8 mm
EndCap-Plastic
Part1^EndCap8Pin-Plastic x 8
PCPinED11075_4639 x 8
91832A115_MIL SPEC. TIN-PLATED BRASS FLAT WASHER
Part2^EndCap8Pin-Plastic
pcbspacerEnd
CopperBraidContact

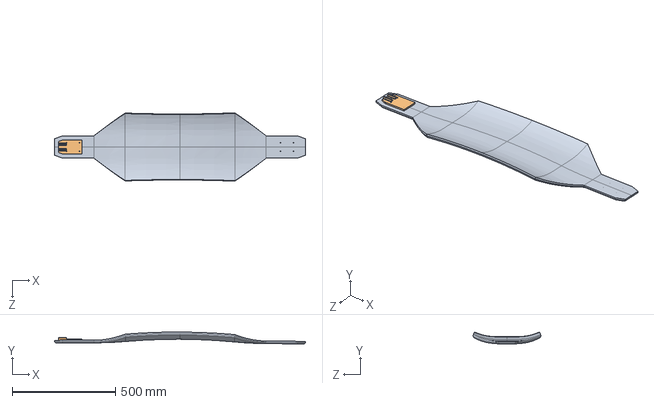
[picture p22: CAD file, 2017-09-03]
CAD/MarkII/Bumper/Assem2.SLDASM
1218.0 x 57.7 x 331.5 mm
boardv6
Part9^Assem2

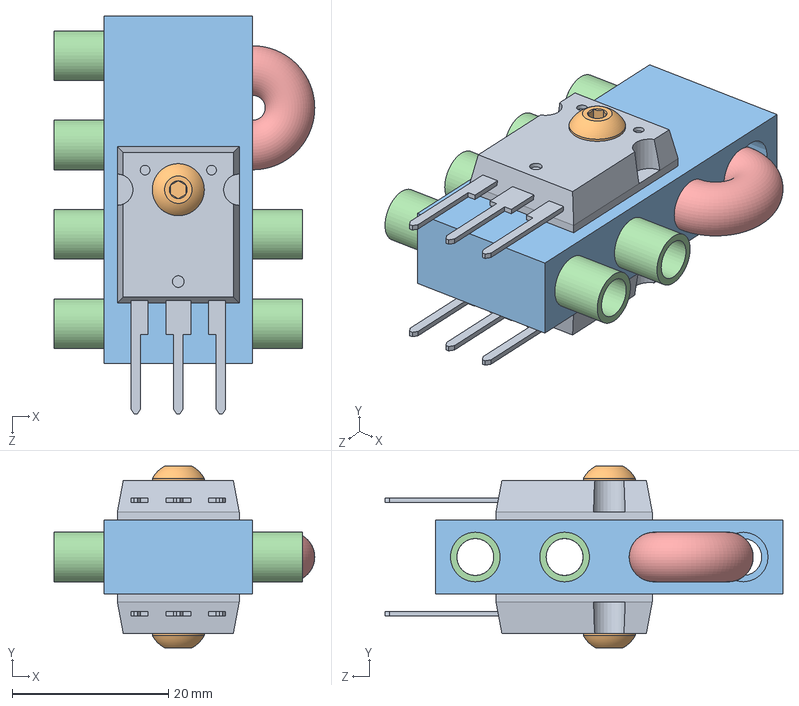
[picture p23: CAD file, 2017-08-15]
CAD/MarkII/Charger/SingleHeatSinkAssem.SLDASM
33.3 x 23.2 x 50.9 mm
TO-247 x 2
Hex_SAE_6-32x.375in_Round x 2
IGBTHeatSink
Copper Pipe .1875ODx.375in x 6
CopperU

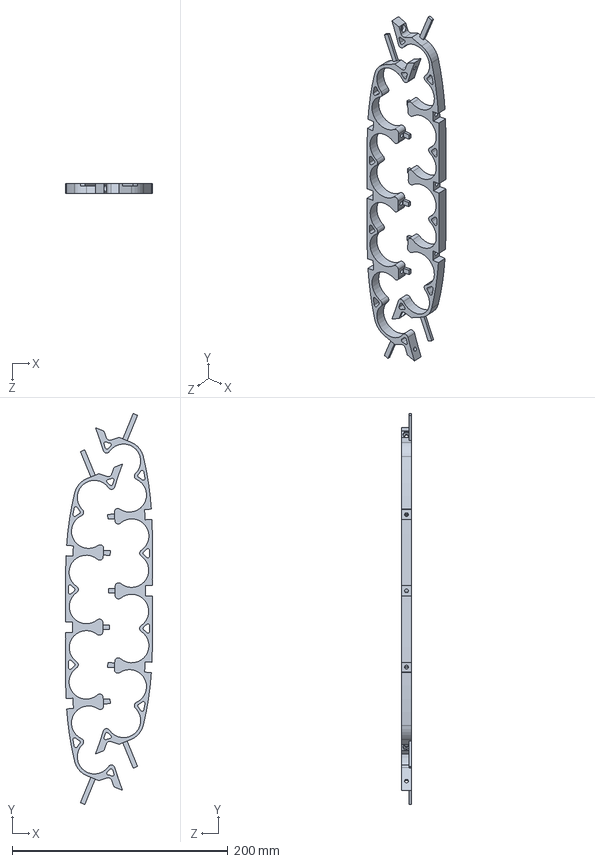
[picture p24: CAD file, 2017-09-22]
CAD/MarkII/CNC/Contoured Battery holder V6 dual.SLDASM
80.4 x 362.2 x 9.53 mm
Contoured Battery holder clip_6V4T&PAcrylCNC x 2

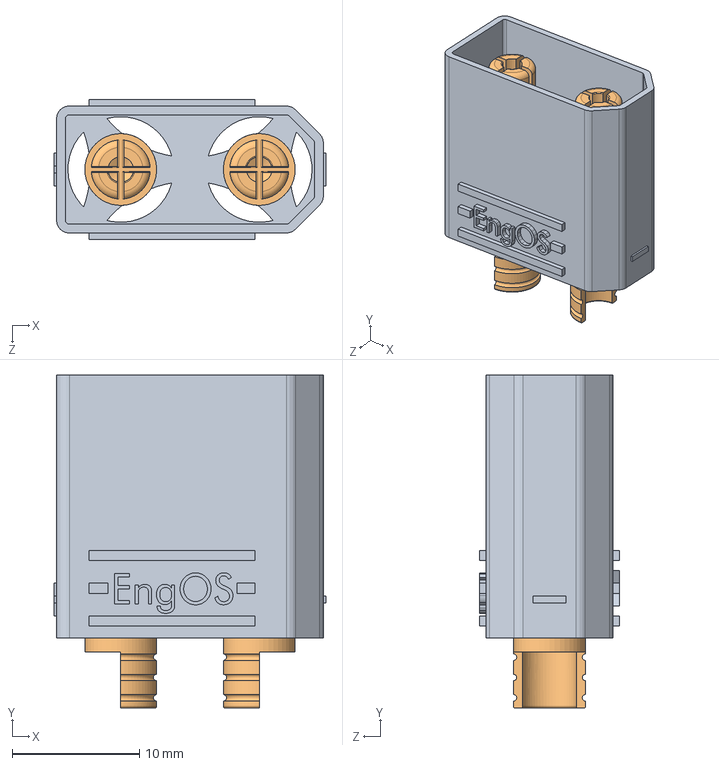
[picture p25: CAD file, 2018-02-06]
CAD/MarkII/Components/XT90/XT90 MALE.SLDASM
21.4 x 26.2 x 11.0 mm
XT90Male_Cover
XT90_MALE_PIN x 2

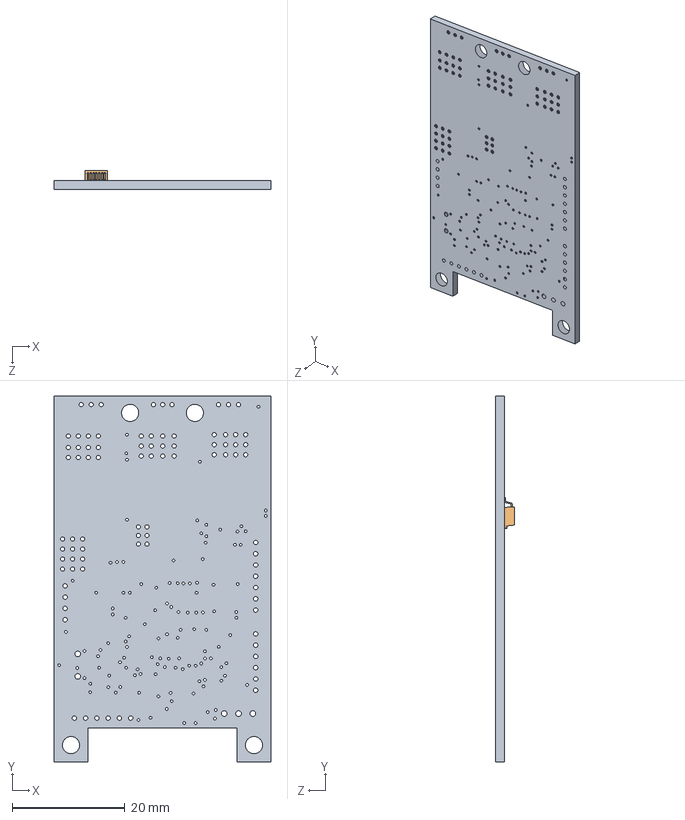
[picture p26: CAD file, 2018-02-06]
CAD/MarkII/Vesc/Vesc.SLDASM
38.5 x 65.0 x 3.38 mm
Boardbldc_4
smd_trans_d2-pak-7

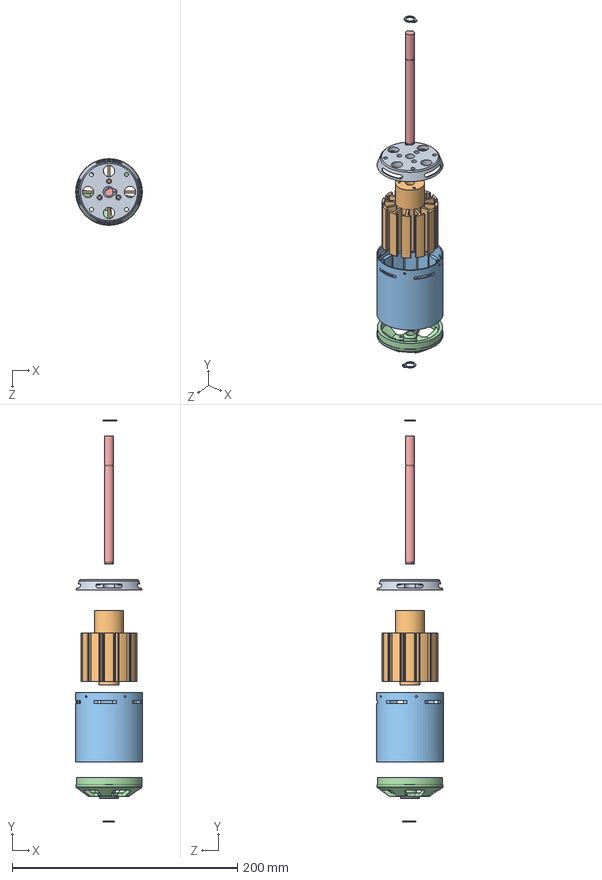
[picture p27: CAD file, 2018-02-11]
CAD/MarkII/Turnigy6374/Turnigy6374.SLDASM
59.1 x 356.8 x 59.1 mm
Stator
StatorPart2
AxelHoldCover
AxelHold
AxisCust
90967A120_STAINLESS STEEL EXTERNAL RETAINING RING x 2

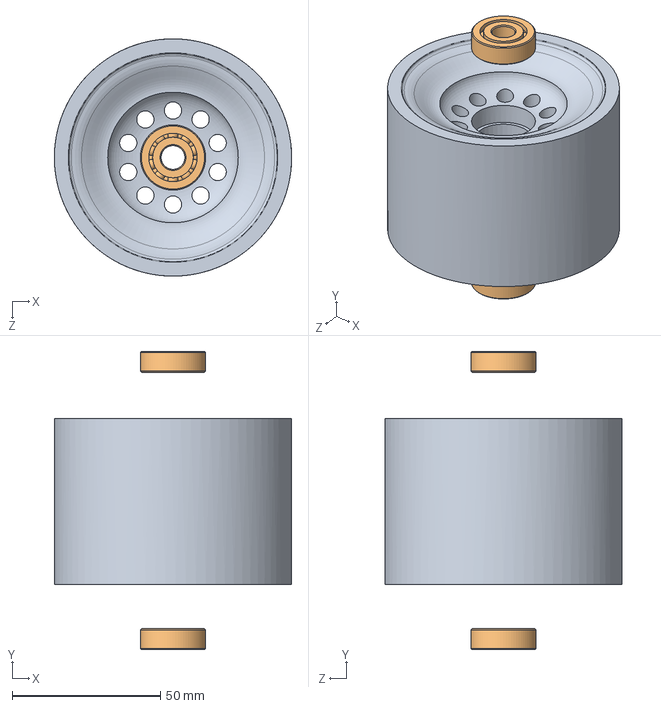
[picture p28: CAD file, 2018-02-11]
CAD/MarkII/Wheel/KegelWheelAssembly.SLDASM
80.0 x 100.4 x 80.0 mm
Kegel 80mm longboard wheel
608-bearing x 2

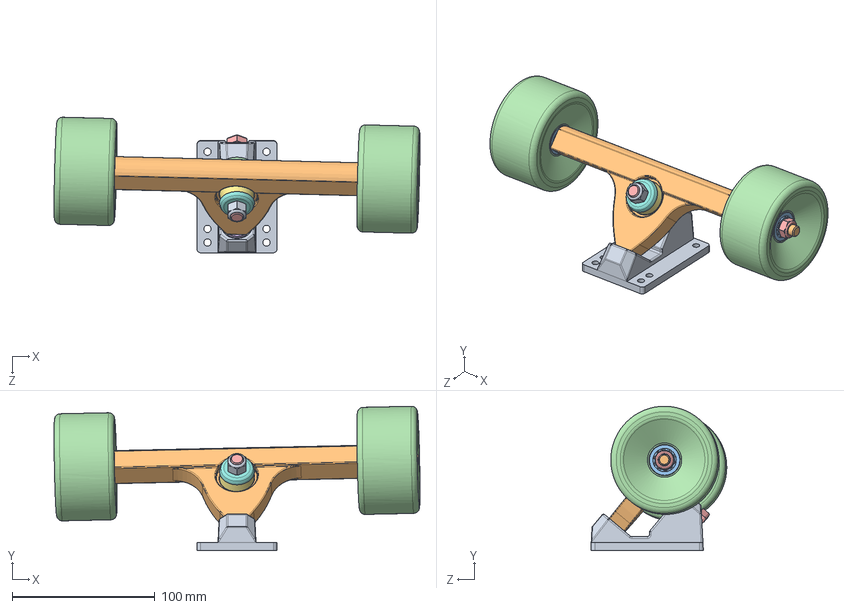
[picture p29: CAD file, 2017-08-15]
CAD/ELongboard STL_CAD/caliber 50/50_CAL/50cal_truck.SLDASM
256.1 x 101.1 x 94.9 mm
50cal_baseplate
10cal_hanger
BS_bushing
BS_washer
kingpin
Pivot_cup
RS_bushing
RS_washer
kingpin-nut
washer x 4
608-bearing x 4
Durian-Wheel x 2
Axle-nut x 2

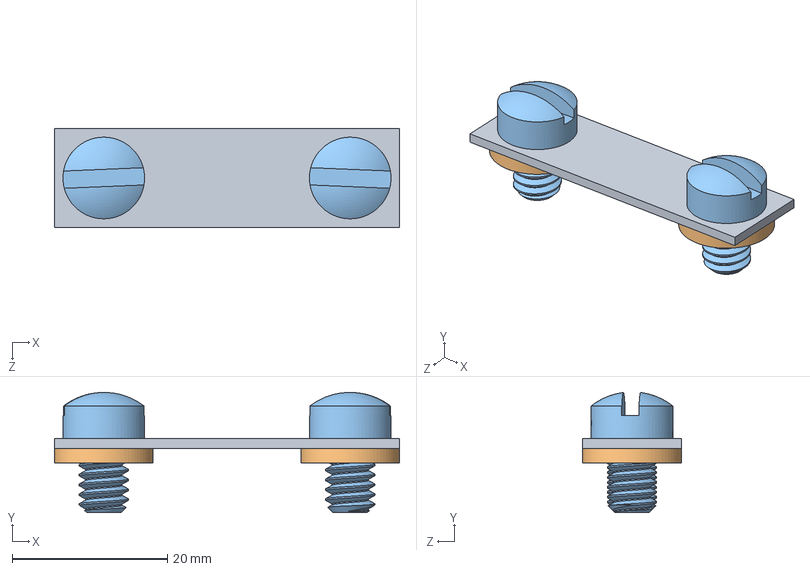
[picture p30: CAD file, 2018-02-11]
CAD/MarkII/BatteryPack/BusBar1.SLDASM
44.5 x 15.5 x 12.7 mm
BusBar1
91832A115_MIL SPEC. TIN-PLATED BRASS FLAT WASHER x 2
90114A608_BRASS FILLISTER HEAD SLOTTED MACHINE SCREW x 2

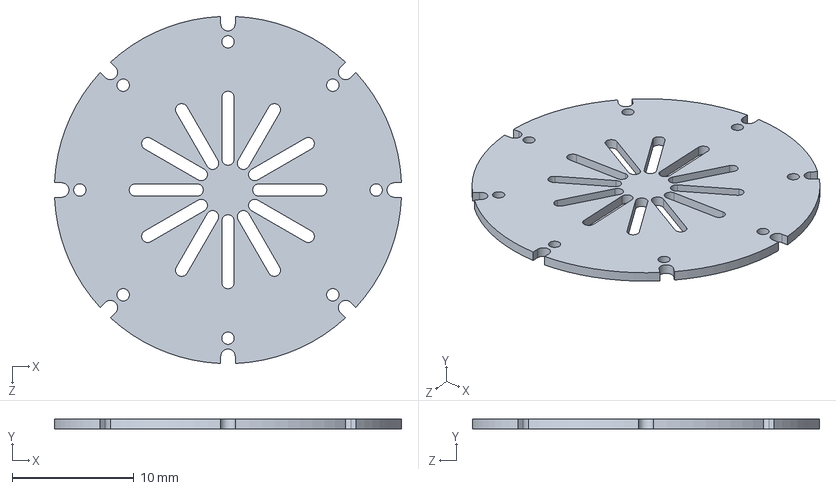
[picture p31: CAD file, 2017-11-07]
CAD/MarkII/BatteryPack/Tubular pack/Spacers/Assem2.SLDASM
28.5 x 0.8 x 28.5 mm

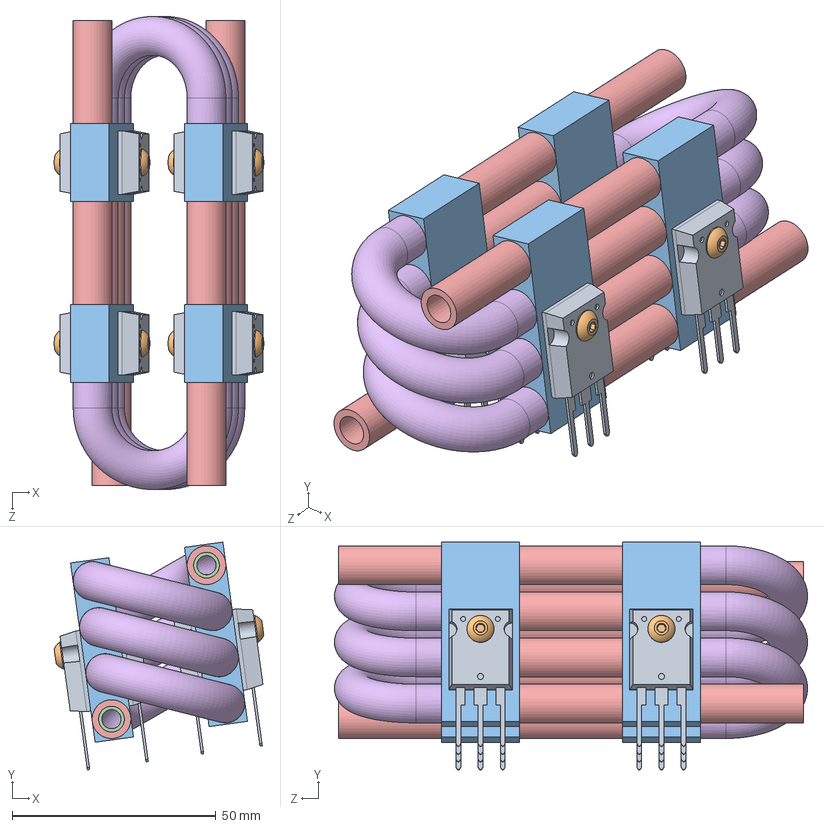
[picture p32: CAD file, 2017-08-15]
CAD/MarkII/Charger/FullAssemblyCharger.SLDASM
51.5 x 56.0 x 116.2 mm
TO-247 x 8
Hex_SAE_6-32x.375in_Round x 8
IGBTHeatSink x 4
Copper Pipe .1875ODx.375in x 32
ClearPVC.375OD.24IDx1in x 12
ClearPVC.375OD.24IDxradius .6in_180 x 6

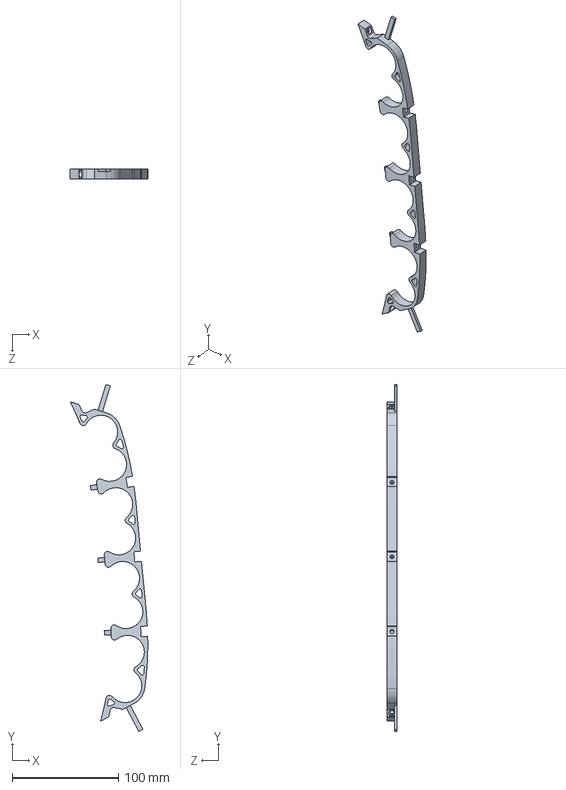
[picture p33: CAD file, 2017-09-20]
CAD/MarkII/CNC/Contoured Battery holder V6 single.SLDASM
73.2 x 327.1 x 9.53 mm

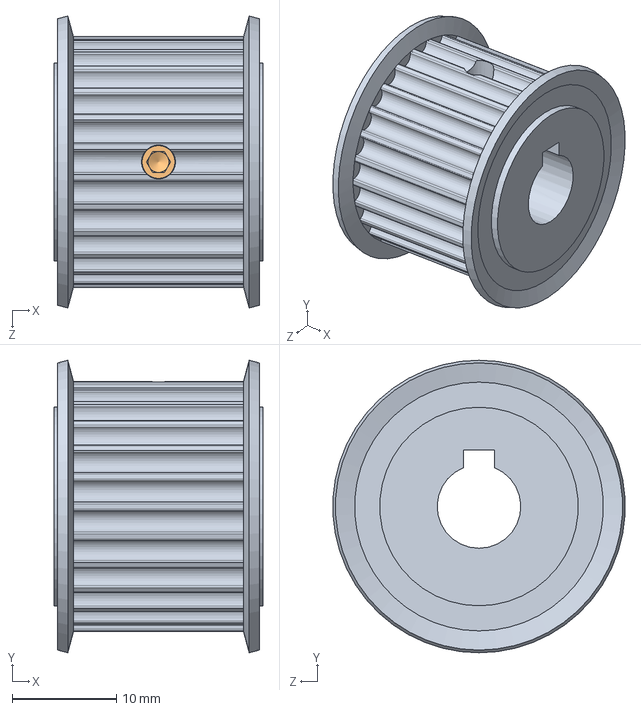
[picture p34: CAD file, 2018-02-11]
CAD/MarkII/PulleyBelts/GPA26GT3150-A-N8.sldasm
20.0 x 28.0 x 27.9 mm
GPA26GT3150-A-N8_b
SET-SCREW4-3 x 2

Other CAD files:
CAD/MarkII/Vesc/VESC_Board_Dummy/files/vesc.SLDASM
CAD/MarkII/BatteryPack/BusBar1Aluminum.SLDASM
CAD/MarkII/Components/XT90/CAD - Shortcut.lnk.SLDASM
CAD/MarkII/Vesc/Board.SLDASM
CAD/ELongboard STL_CAD/caliber 50/50_CAL/10cal_hanger.SLDPRT
CAD/ELongboard STL_CAD/caliber 50/50_CAL/50cal_baseplate.SLDPRT
CAD/ELongboard STL_CAD/caliber 50/50_CAL/608-bearing.SLDPRT
CAD/ELongboard STL_CAD/caliber 50/50_CAL/Axle-nut.SLDPRT
CAD/ELongboard STL_CAD/caliber 50/50_CAL/BS_bushing.SLDPRT
CAD/ELongboard STL_CAD/caliber 50/50_CAL/BS_washer.SLDPRT
CAD/ELongboard STL_CAD/caliber 50/50_CAL/Durian-Wheel.SLDPRT
CAD/ELongboard STL_CAD/caliber 50/50_CAL/Pivot_cup.SLDPRT
CAD/ELongboard STL_CAD/caliber 50/50_CAL/RS_bushing.SLDPRT
CAD/ELongboard STL_CAD/caliber 50/50_CAL/RS_washer.SLDPRT
CAD/ELongboard STL_CAD/caliber 50/50_CAL/kingpin-nut.SLDPRT
CAD/ELongboard STL_CAD/caliber 50/50_CAL/kingpin.SLDPRT
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

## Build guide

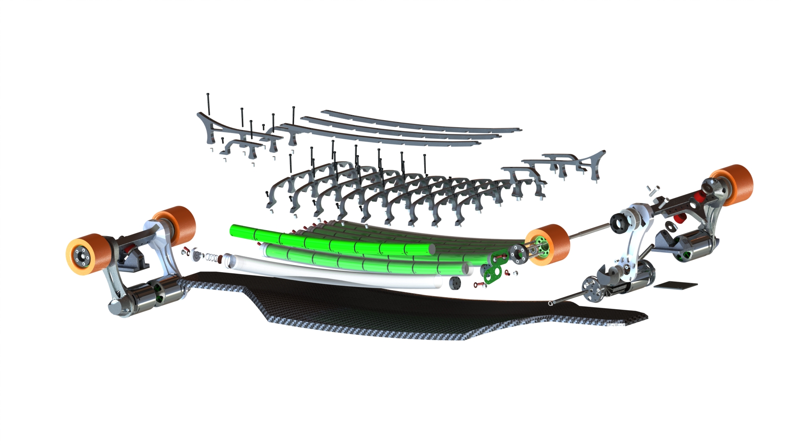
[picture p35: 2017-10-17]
Pictures/Full Assembly Exploded 3.JPG

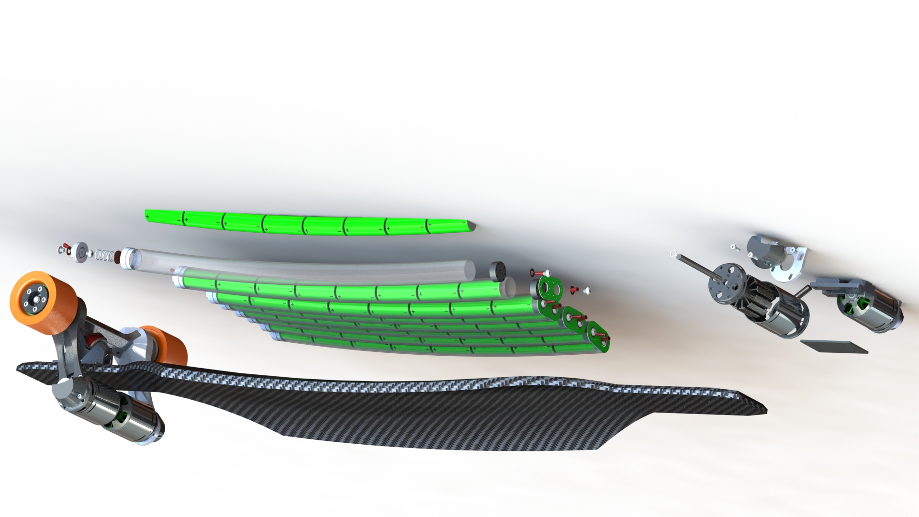
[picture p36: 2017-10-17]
Pictures/Full Assembly Exploded 1.JPG

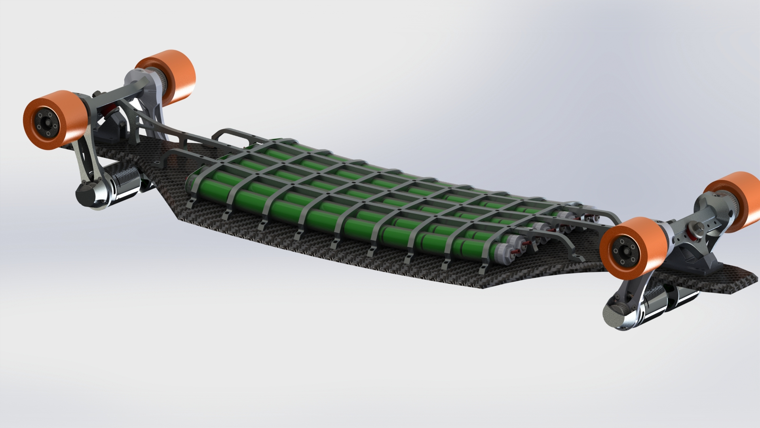
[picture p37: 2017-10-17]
Pictures/Full Assembly .JPG

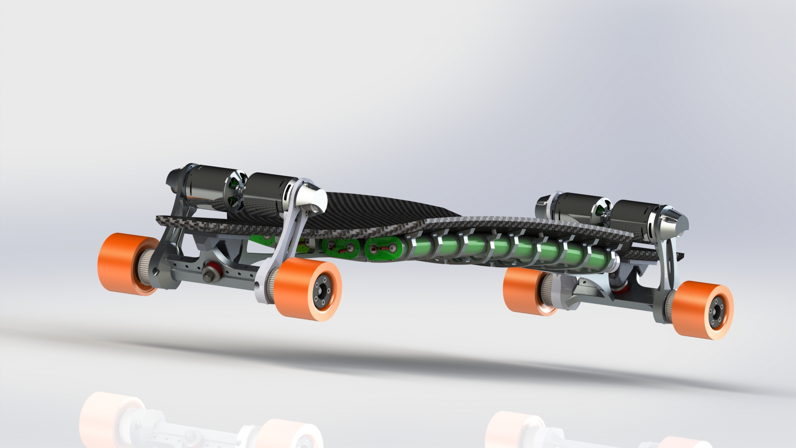
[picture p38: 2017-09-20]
Pictures/Full Assembly V12_2.JPG

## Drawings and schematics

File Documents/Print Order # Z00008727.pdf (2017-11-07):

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

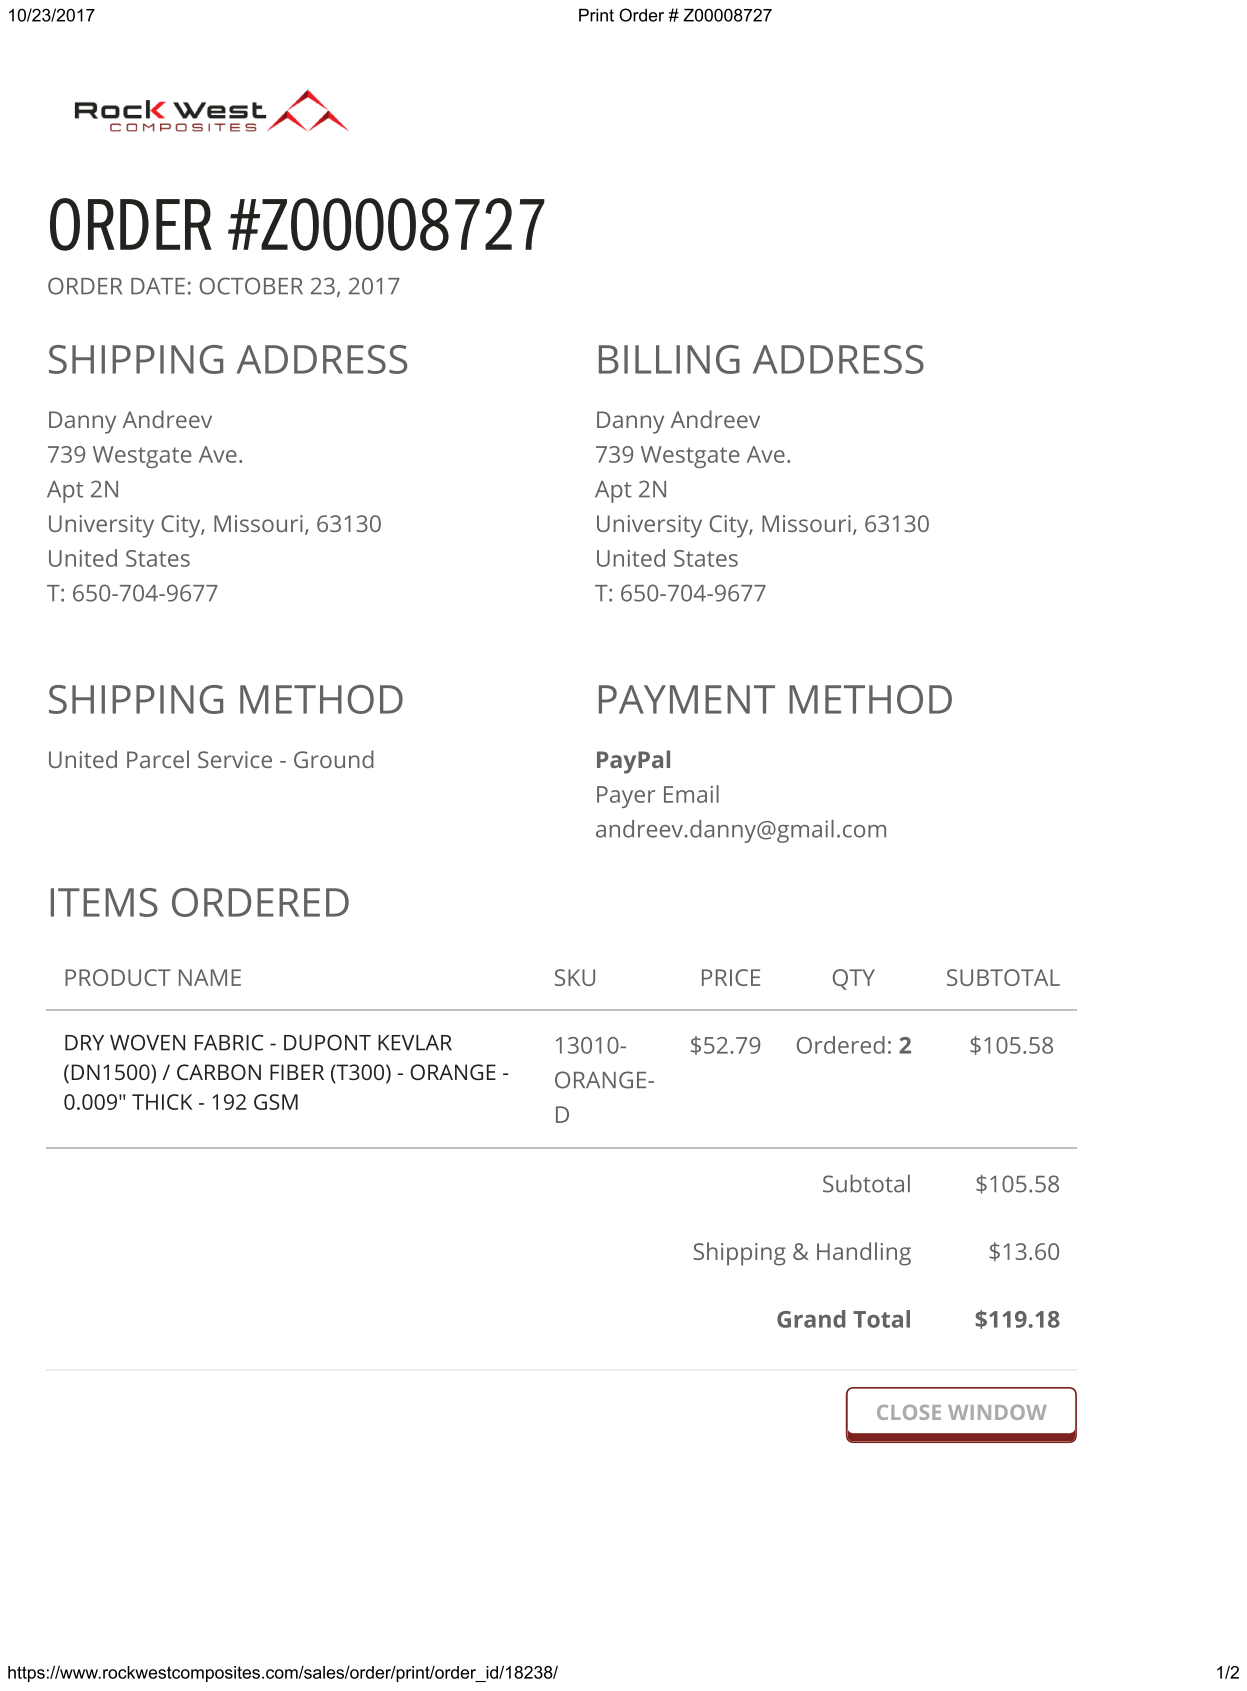
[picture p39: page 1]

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

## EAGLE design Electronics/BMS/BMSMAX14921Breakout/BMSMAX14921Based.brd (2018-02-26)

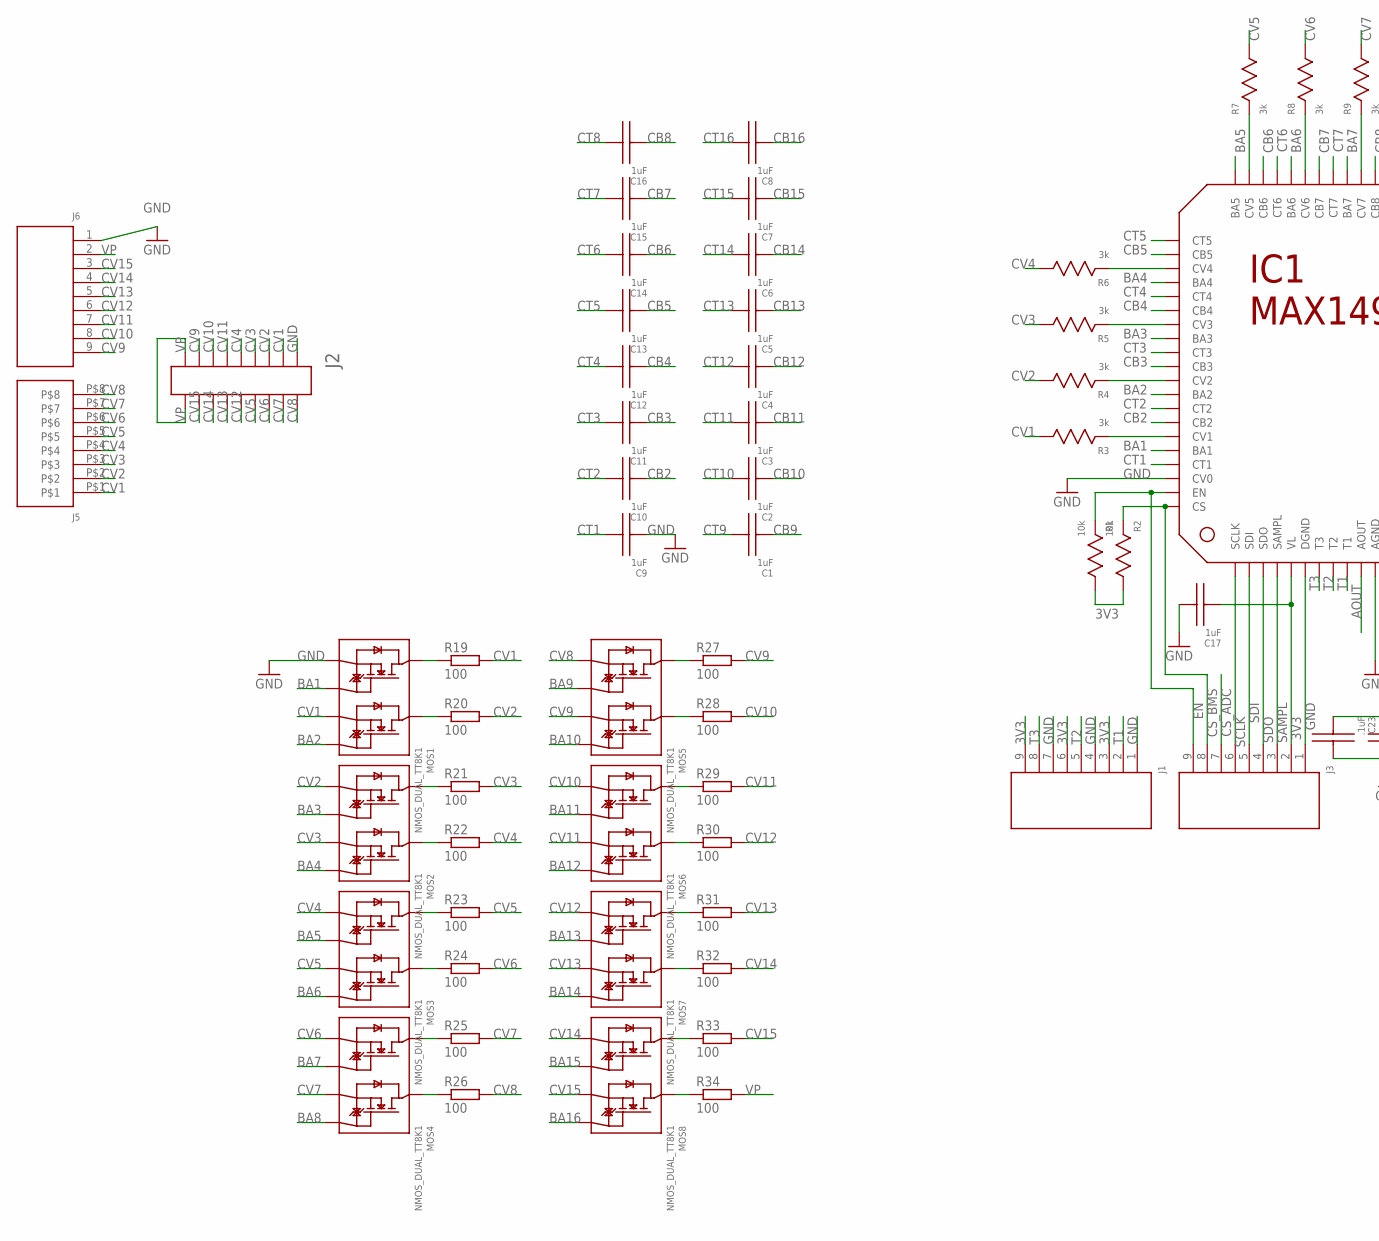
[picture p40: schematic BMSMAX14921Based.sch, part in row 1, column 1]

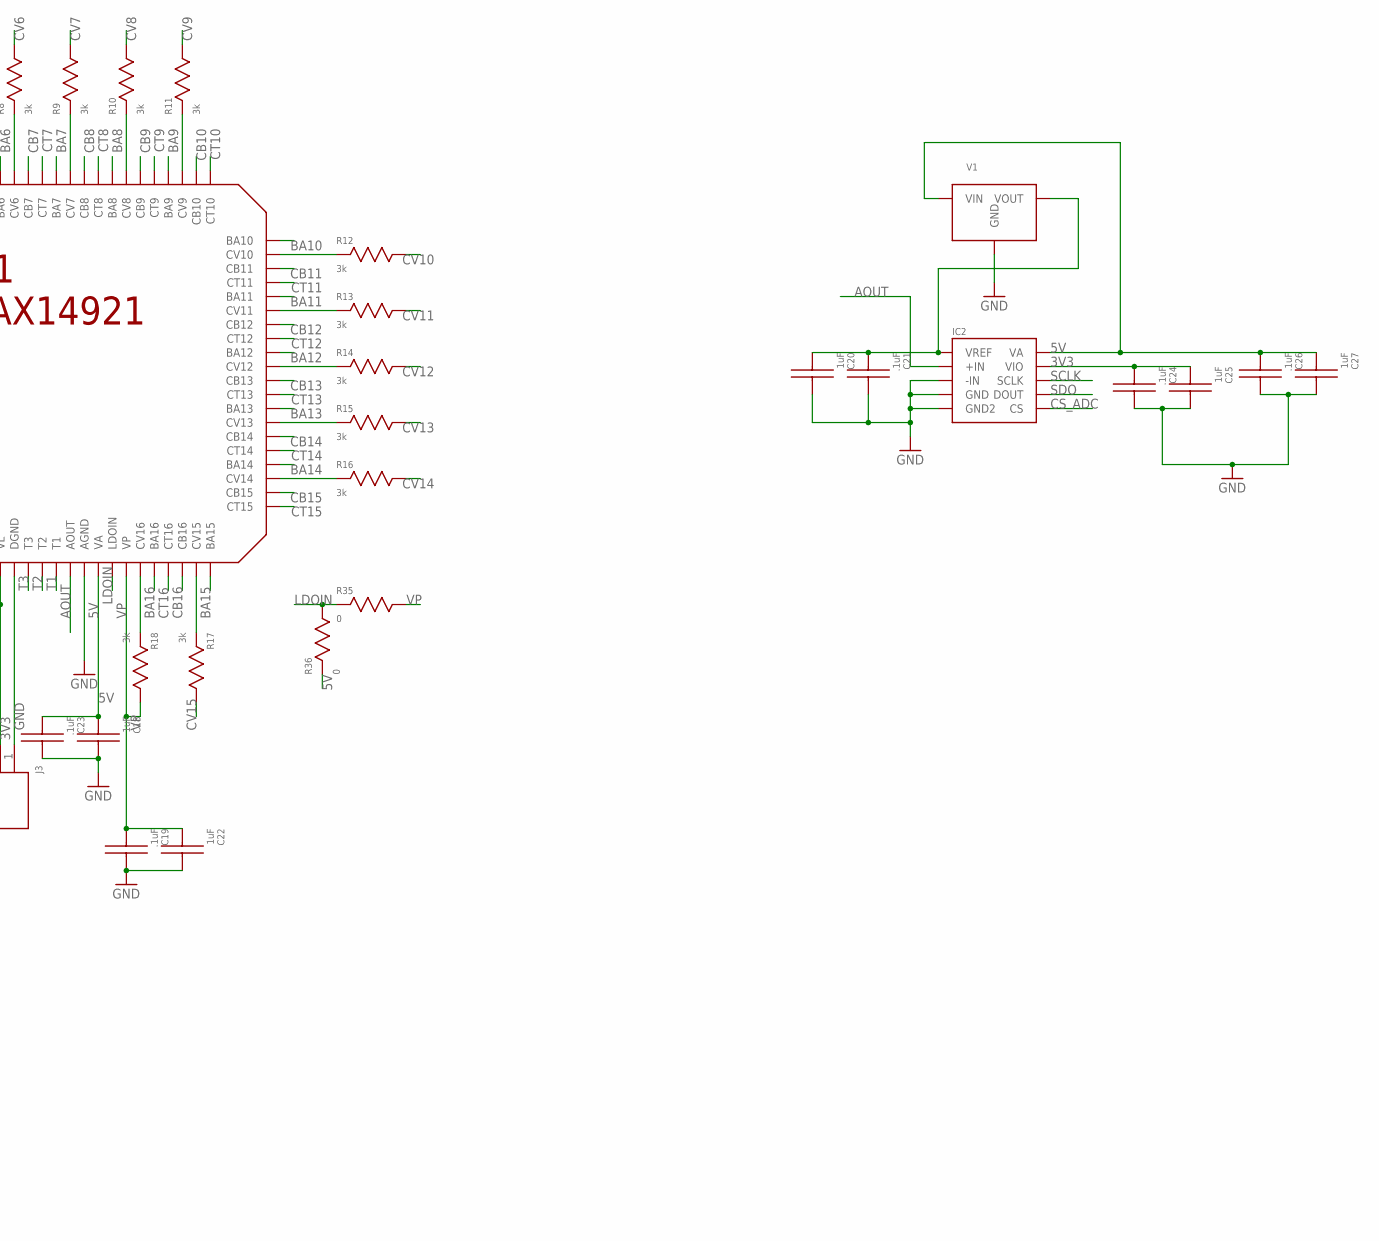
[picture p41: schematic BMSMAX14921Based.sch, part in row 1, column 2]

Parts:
C1, C2, C3, C4, C5, C6, C7, C8, C9, C10, C11, C12, C13, C14, C15, C16, C17, C18, C20, C22, C25, C27: 1uF; 0805_(2012_METRIC)
C19, C21, C23, C24, C26: .1uF; 0805_(2012_METRIC)
IC1: MAX14921; 80TQFP
IC2: ADC141S626; 10-VSSOP
J1, J3, J6: CONNECTOR_9PIN; 9PIN_.1'
J2: CONNECTORJST2X9_2MM; CONNECTOR9X2_2MMPITCH
J5: CONNECTOR_8PIN; 8PIN_.1'
MOS1, MOS2, MOS3, MOS4, MOS5, MOS6, MOS7, MOS8: NMOS_DUAL_TT8K1; TSST8
R1, R2: 10k; 0805_(2012_METRIC)
R3, R4, R5, R6, R7, R8, R9, R10, R11, R12, R13, R14, R15, R16, R17, R18: 3k; 0805_(2012_METRIC)
R19, R20, R21, R22, R23, R24, R25, R26, R27, R28, R29, R30, R31, R32, R33, R34: 100; 0411V
R35, R36: 0; 0805_(2012_METRIC)
V1: REF3040; SOT-23

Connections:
3V3: C17.P$2, C24.P$2, C25.P$2, IC1.P$5 (VL), IC2.P$9 (VIO), J1.3, J1.6, J1.9, J3.2, R1.P$1, R2.P$1
5V: C18.P$2, C23.P$2, C26.P$2, C27.P$2, IC1.P$12 (VA), IC2.P$10 (VA), R36.P$2, V1.1 (VIN)
AOUT: IC1.P$10 (AOUT), IC2.P$2 (+IN)
BA1: IC1.P$76 (BA1), MOS1.P$2 (G1)
BA2: IC1.P$72 (BA2), MOS1.P$4 (G2)
BA3: IC1.P$68 (BA3), MOS2.P$2 (G1)
BA4: IC1.P$64 (BA4), MOS2.P$4 (G2)
BA5: IC1.P$60 (BA5), MOS3.P$2 (G1)
BA6: IC1.P$56 (BA6), MOS3.P$4 (G2)
BA7: IC1.P$52 (BA7), MOS4.P$2 (G1)
BA8: IC1.P$48 (BA8), MOS4.P$4 (G2)
BA9: IC1.P$44 (BA9), MOS5.P$2 (G1)
BA10: IC1.P$40 (BA10), MOS5.P$4 (G2)
BA11: IC1.P$36 (BA11), MOS6.P$2 (G1)
BA12: IC1.P$32 (BA12), MOS6.P$4 (G2)
BA13: IC1.P$28 (BA13), MOS7.P$2 (G1)
BA14: IC1.P$24 (BA14), MOS7.P$4 (G2)
BA15: IC1.P$20 (BA15), MOS8.P$2 (G1)
BA16: IC1.P$16 (BA16), MOS8.P$4 (G2)
CB2: C10.P$2, IC1.P$74 (CB2)
CB3: C11.P$2, IC1.P$70 (CB3)
CB4: C12.P$2, IC1.P$66 (CB4)
CB5: C13.P$2, IC1.P$62 (CB5)
CB6: C14.P$2, IC1.P$58 (CB6)
CB7: C15.P$2, IC1.P$54 (CB7)
CB8: C16.P$2, IC1.P$50 (CB8)
CB9: C1.P$2, IC1.P$46 (CB9)
CB10: C2.P$2, IC1.P$42 (CB10)
CB11: C3.P$2, IC1.P$38 (CB11)
CB12: C4.P$2, IC1.P$34 (CB12)
CB13: C5.P$2, IC1.P$30 (CB13)
CB14: C6.P$2, IC1.P$26 (CB14)
CB15: C7.P$2, IC1.P$22 (CB15)
CB16: C8.P$2, IC1.P$18 (CB16)
CS_ADC: IC2.P$6 (CS), J3.7
CS_BMS: IC1.P$80 (CS), J3.8, R2.P$2
CT1: C9.P$1, IC1.P$77 (CT1)
CT2: C10.P$1, IC1.P$73 (CT2)
CT3: C11.P$1, IC1.P$69 (CT3)
CT4: C12.P$1, IC1.P$65 (CT4)
CT5: C13.P$1, IC1.P$61 (CT5)
CT6: C14.P$1, IC1.P$57 (CT6)
CT7: C15.P$1, IC1.P$53 (CT7)
CT8: C16.P$1, IC1.P$49 (CT8)
CT9: C1.P$1, IC1.P$45 (CT9)
CT10: C2.P$1, IC1.P$41 (CT10)
CT11: C3.P$1, IC1.P$37 (CT11)
CT12: C4.P$1, IC1.P$33 (CT12)
CT13: C5.P$1, IC1.P$29 (CT13)
CT14: C6.P$1, IC1.P$25 (CT14)
CT15: C7.P$1, IC1.P$21 (CT15)
CT16: C8.P$1, IC1.P$17 (CT16)
CV1: J2.P$2, J5.P$1, MOS1.P$3 (S2), R3.P$1, R19.2
CV2: J2.P$3, J5.P$2, MOS2.P$1 (S1), R4.P$1, R20.2
CV3: J2.P$4, J5.P$3, MOS2.P$3 (S2), R5.P$1, R21.2
CV4: J2.P$5, J5.P$4, MOS3.P$1 (S1), R6.P$1, R22.2
CV5: J2.P$15, J5.P$5, MOS3.P$3 (S2), R7.P$1, R23.2
CV6: J2.P$16, J5.P$6, MOS4.P$1 (S1), R8.P$1, R24.2
CV7: J2.P$17, J5.P$7, MOS4.P$3 (S2), R9.P$1, R25.2
CV8: J2.P$18, J5.P$8, MOS5.P$1 (S1), R10.P$1, R26.2
CV9: J2.P$8, J6.9, MOS5.P$3 (S2), R11.P$1, R27.2
CV10: J2.P$7, J6.8, MOS6.P$1 (S1), R12.P$1, R28.2
CV11: J2.P$6, J6.7, MOS6.P$3 (S2), R13.P$1, R29.2
CV12: J2.P$14, J6.6, MOS7.P$1 (S1), R14.P$1, R30.2
CV13: J2.P$13, J6.5, MOS7.P$3 (S2), R15.P$1, R31.2
CV14: J2.P$12, J6.4, MOS8.P$1 (S1), R16.P$1, R32.2
CV15: J2.P$11, J6.3, MOS8.P$3 (S2), R17.P$1, R33.2
EN: IC1.P$79 (EN), J3.9, R1.P$2
GND: C9.P$2, C17.P$1, C18.P$1, C19.P$1, C20.P$1, C21.P$1, C22.P$1, C23.P$1, C24.P$1, C25.P$1, C26.P$1, C27.P$1, IC1.P$6 (DGND), IC1.P$11 (AGND), IC1.P$78 (CV0), IC2.P$3 (-IN), IC2.P$4 (GND), IC2.P$5 (GND2), J1.1, J1.4, J1.7, J2.P$1, J3.1, J6.1, MOS1.P$1 (S1), V1.3 (GND)
LDOIN: IC1.P$13 (LDOIN), R35.P$2, R36.P$1
unnamed: MOS1.P$7 (D1), MOS1.P$8 (D1), R19.1
unnamed: C20.P$2, C21.P$2, IC2.P$1 (VREF), V1.2 (VOUT)
unnamed: IC1.P$71 (CV2), R4.P$2
unnamed: IC1.P$67 (CV3), R5.P$2
unnamed: IC1.P$75 (CV1), R3.P$2
unnamed: IC1.P$63 (CV4), R6.P$2
unnamed: IC1.P$59 (CV5), R7.P$2
unnamed: IC1.P$55 (CV6), R8.P$2
unnamed: IC1.P$51 (CV7), R9.P$2
unnamed: IC1.P$47 (CV8), R10.P$2
unnamed: IC1.P$43 (CV9), R11.P$2
unnamed: IC1.P$39 (CV10), R12.P$2
unnamed: IC1.P$35 (CV11), R13.P$2
unnamed: IC1.P$31 (CV12), R14.P$2
unnamed: IC1.P$27 (CV13), R15.P$2
unnamed: IC1.P$23 (CV14), R16.P$2
unnamed: IC1.P$19 (CV15), R17.P$2
unnamed: IC1.P$15 (CV16), R18.P$2
unnamed: MOS1.P$5 (D2), MOS1.P$6 (D2), R20.1
unnamed: MOS2.P$7 (D1), MOS2.P$8 (D1), R21.1
unnamed: MOS2.P$5 (D2), MOS2.P$6 (D2), R22.1
unnamed: MOS3.P$7 (D1), MOS3.P$8 (D1), R23.1
unnamed: MOS3.P$5 (D2), MOS3.P$6 (D2), R24.1
unnamed: MOS4.P$7 (D1), MOS4.P$8 (D1), R25.1
unnamed: MOS4.P$5 (D2), MOS4.P$6 (D2), R26.1
unnamed: MOS5.P$7 (D1), MOS5.P$8 (D1), R27.1
unnamed: MOS5.P$5 (D2), MOS5.P$6 (D2), R28.1
unnamed: MOS6.P$7 (D1), MOS6.P$8 (D1), R29.1
unnamed: MOS6.P$5 (D2), MOS6.P$6 (D2), R30.1
unnamed: MOS7.P$7 (D1), MOS7.P$8 (D1), R31.1
unnamed: MOS7.P$5 (D2), MOS7.P$6 (D2), R32.1
unnamed: MOS8.P$7 (D1), MOS8.P$8 (D1), R33.1
unnamed: MOS8.P$5 (D2), MOS8.P$6 (D2), R34.1
SAMPL: IC1.P$4 (SAMPL), J3.3
SCLK: IC1.P$1 (SCLK), IC2.P$8 (SCLK), J3.6
SDI: IC1.P$2 (SDI), J3.5
SDO: IC1.P$3 (SDO), IC2.P$7 (DOUT), J3.4
T1: IC1.P$9 (T1), J1.2
T2: IC1.P$8 (T2), J1.5
T3: IC1.P$7 (T3), J1.8
VP: C19.P$2, C22.P$2, IC1.P$14 (VP), J2.P$9, J2.P$10, J6.2, R18.P$1, R34.2, R35.P$1

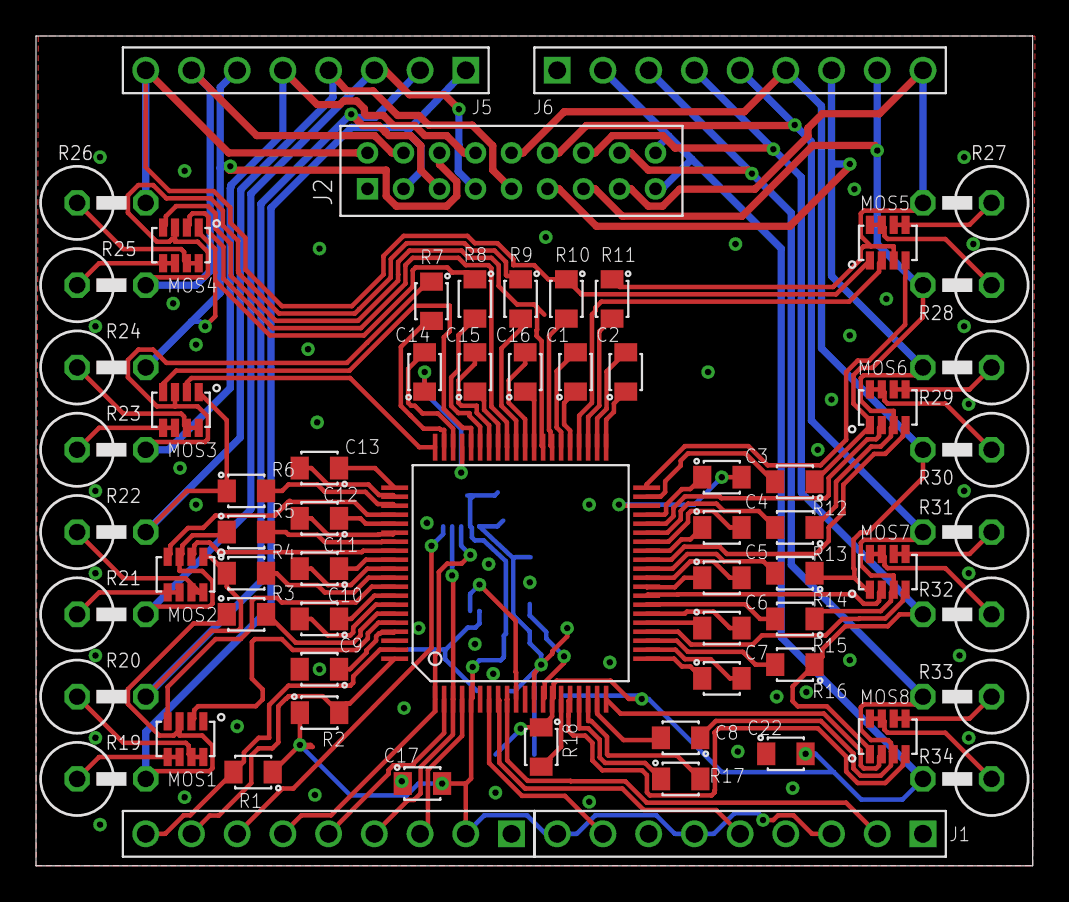
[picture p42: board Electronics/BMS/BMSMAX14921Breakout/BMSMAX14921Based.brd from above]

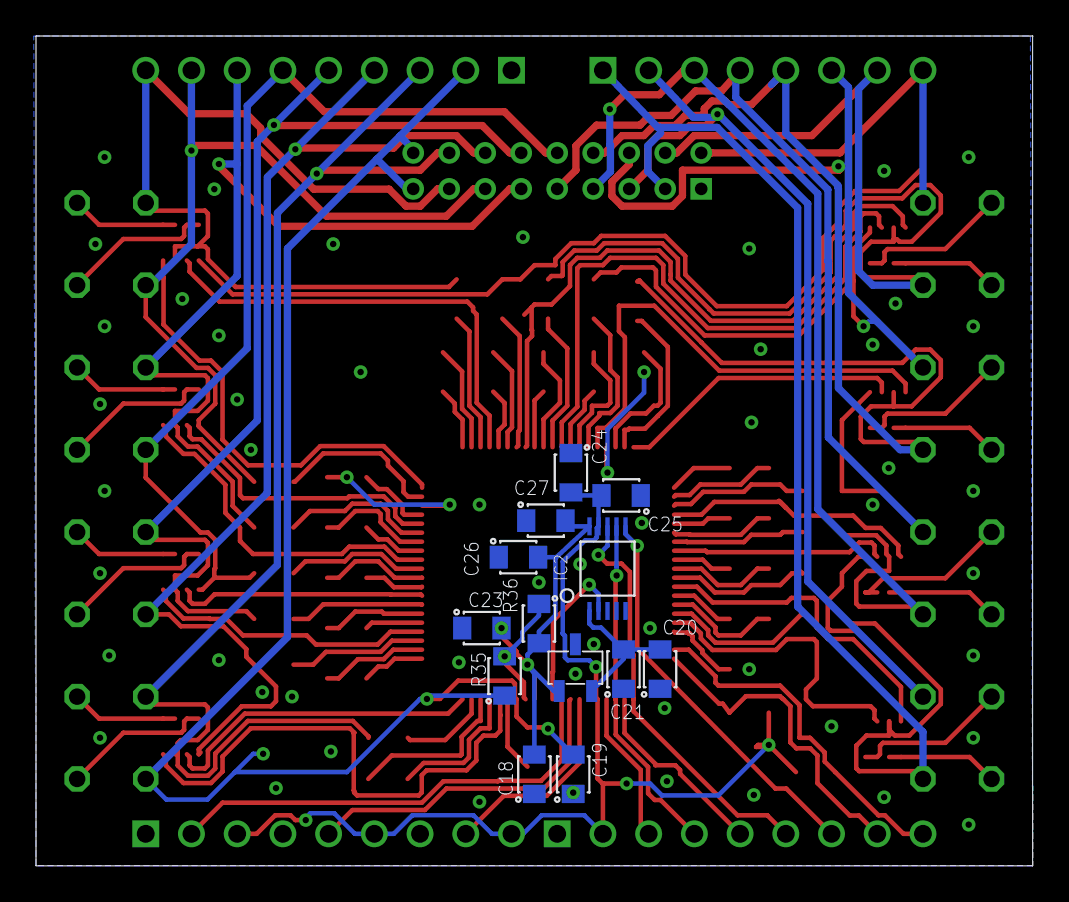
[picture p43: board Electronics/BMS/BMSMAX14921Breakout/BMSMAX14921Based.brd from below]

Board: 2 copper layers, 55.4 x 46.1 mm, 79 parts (13 on the bottom side), 111 nets.

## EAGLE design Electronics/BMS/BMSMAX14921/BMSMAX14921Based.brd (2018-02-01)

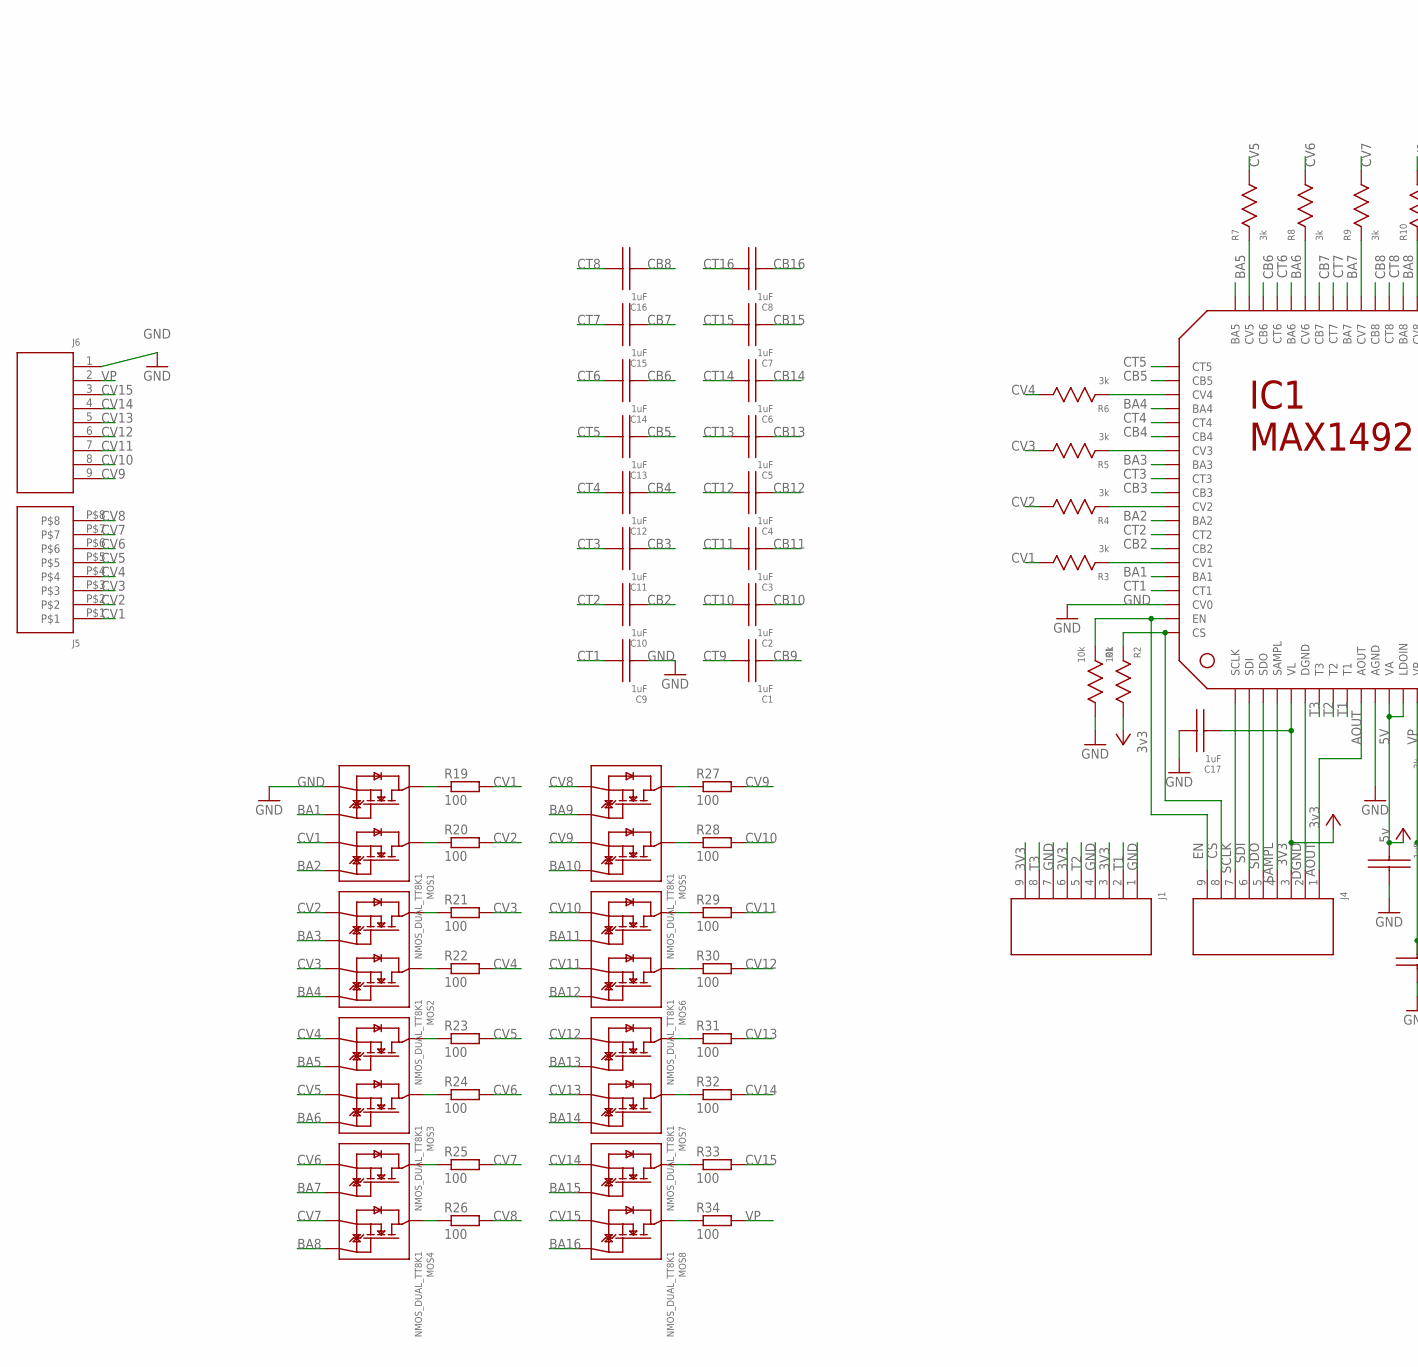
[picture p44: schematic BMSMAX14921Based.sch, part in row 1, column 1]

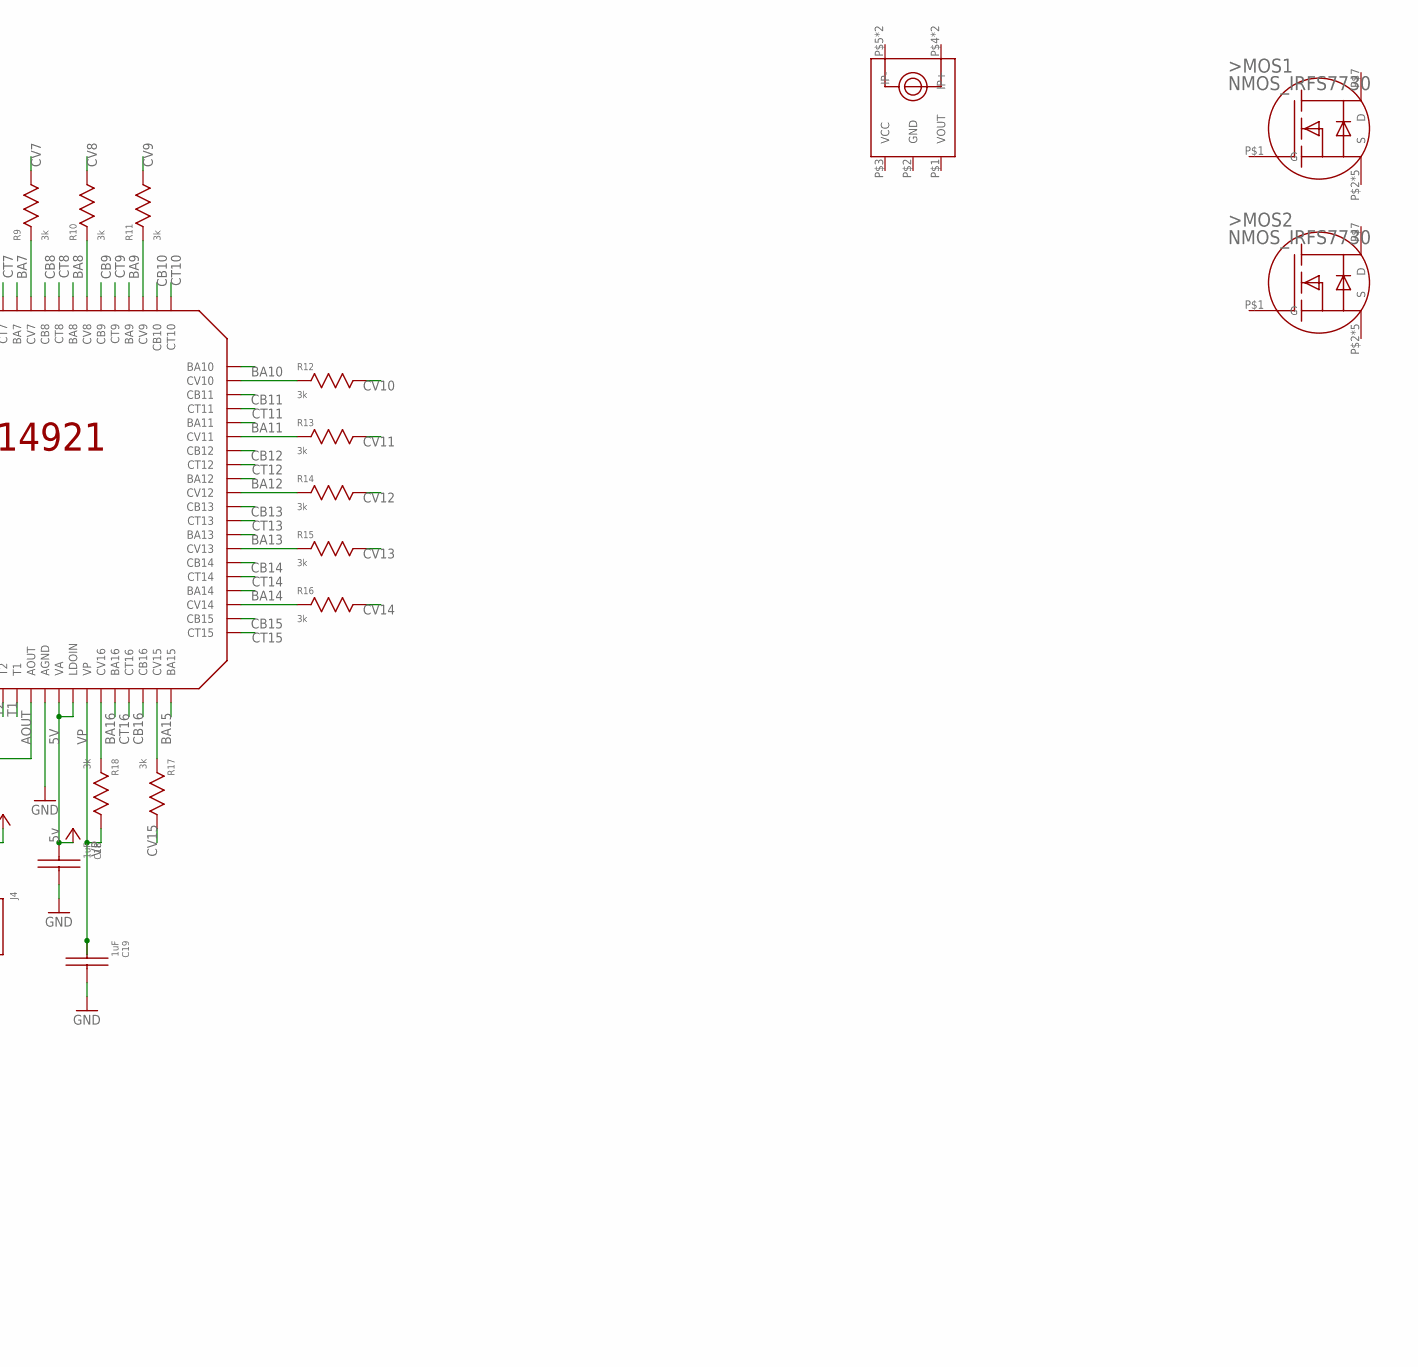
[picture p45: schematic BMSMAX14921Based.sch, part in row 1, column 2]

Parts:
>MOS1, >MOS2: NMOS_IRFS7730; D2PAK-7PIN
C1, C2, C3, C4, C5, C6, C7, C8, C9, C10, C11, C12, C13, C14, C15, C16, C17, C18, C19: 1uF; 0805_(2012_METRIC)
IC1: MAX14921; 80TQFP
J1, J4, J6: CONNECTOR_9PIN; 9PIN_.1'
J5: CONNECTOR_8PIN; 8PIN_.1'
MOS1, MOS2, MOS3, MOS4, MOS5, MOS6, MOS7, MOS8: NMOS_DUAL_TT8K1; TSST8
R1, R2: 10k; 0805_(2012_METRIC)
R3, R4, R5, R6, R7, R8, R9, R10, R11, R12, R13, R14, R15, R16, R17, R18: 3k; 0805_(2012_METRIC)
R19, R20, R21, R22, R23, R24, R25, R26, R27, R28, R29, R30, R31, R32, R33, R34: 100; 0411V
U$1: ACS758XCB; CB5PFF

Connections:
3V3: C17.P$2, IC1.5 (VL), J1.3, J1.6, J1.9, J4.3, R2.P$1
5V: C18.P$2, IC1.12 (VA), IC1.13 (LDOIN)
AOUT: IC1.10 (AOUT), J4.1
BA1: IC1.76 (BA1), MOS1.P$2 (G1)
BA2: IC1.72 (BA2), MOS1.P$4 (G2)
BA3: IC1.68 (BA3), MOS2.P$2 (G1)
BA4: IC1.64 (BA4), MOS2.P$4 (G2)
BA5: IC1.60 (BA5), MOS3.P$2 (G1)
BA6: IC1.56 (BA6), MOS3.P$4 (G2)
BA7: IC1.52 (BA7), MOS4.P$2 (G1)
BA8: IC1.48 (BA8), MOS4.P$4 (G2)
BA9: IC1.44 (BA9), MOS5.P$2 (G1)
BA10: IC1.40 (BA10), MOS5.P$4 (G2)
BA11: IC1.36 (BA11), MOS6.P$2 (G1)
BA12: IC1.32 (BA12), MOS6.P$4 (G2)
BA13: IC1.28 (BA13), MOS7.P$2 (G1)
BA14: IC1.24 (BA14), MOS7.P$4 (G2)
BA15: IC1.20 (BA15), MOS8.P$2 (G1)
BA16: IC1.16 (BA16), MOS8.P$4 (G2)
CB2: C10.P$2, IC1.74 (CB2)
CB3: C11.P$2, IC1.70 (CB3)
CB4: C12.P$2, IC1.66 (CB4)
CB5: C13.P$2, IC1.62 (CB5)
CB6: C14.P$2, IC1.58 (CB6)
CB7: C15.P$2, IC1.54 (CB7)
CB8: C16.P$2, IC1.50 (CB8)
CB9: C1.P$2, IC1.46 (CB9)
CB10: C2.P$2, IC1.42 (CB10)
CB11: C3.P$2, IC1.38 (CB11)
CB12: C4.P$2, IC1.34 (CB12)
CB13: C5.P$2, IC1.30 (CB13)
CB14: C6.P$2, IC1.26 (CB14)
CB15: C7.P$2, IC1.22 (CB15)
CB16: C8.P$2, IC1.18 (CB16)
CS: IC1.80 (CS), J4.8, R2.P$2
CT1: C9.P$1, IC1.77 (CT1)
CT2: C10.P$1, IC1.73 (CT2)
CT3: C11.P$1, IC1.69 (CT3)
CT4: C12.P$1, IC1.65 (CT4)
CT5: C13.P$1, IC1.61 (CT5)
CT6: C14.P$1, IC1.57 (CT6)
CT7: C15.P$1, IC1.53 (CT7)
CT8: C16.P$1, IC1.49 (CT8)
CT9: C1.P$1, IC1.45 (CT9)
CT10: C2.P$1, IC1.41 (CT10)
CT11: C3.P$1, IC1.37 (CT11)
CT12: C4.P$1, IC1.33 (CT12)
CT13: C5.P$1, IC1.29 (CT13)
CT14: C6.P$1, IC1.25 (CT14)
CT15: C7.P$1, IC1.21 (CT15)
CT16: C8.P$1, IC1.17 (CT16)
CV1: J5.P$1, MOS1.P$3 (S2), R3.P$1, R19.2
CV2: J5.P$2, MOS2.P$1 (S1), R4.P$1, R20.2
CV3: J5.P$3, MOS2.P$3 (S2), R5.P$1, R21.2
CV4: J5.P$4, MOS3.P$1 (S1), R6.P$1, R22.2
CV5: J5.P$5, MOS3.P$3 (S2), R7.P$1, R23.2
CV6: J5.P$6, MOS4.P$1 (S1), R8.P$1, R24.2
CV7: J5.P$7, MOS4.P$3 (S2), R9.P$1, R25.2
CV8: J5.P$8, MOS5.P$1 (S1), R10.P$1, R26.2
CV9: J6.9, MOS5.P$3 (S2), R11.P$1, R27.2
CV10: J6.8, MOS6.P$1 (S1), R12.P$1, R28.2
CV11: J6.7, MOS6.P$3 (S2), R13.P$1, R29.2
CV12: J6.6, MOS7.P$1 (S1), R14.P$1, R30.2
CV13: J6.5, MOS7.P$3 (S2), R15.P$1, R31.2
CV14: J6.4, MOS8.P$1 (S1), R16.P$1, R32.2
CV15: J6.3, MOS8.P$3 (S2), R17.P$1, R33.2
DGND: IC1.6 (DGND), J4.2
EN: IC1.79 (EN), J4.9, R1.P$2
GND: C9.P$2, C17.P$1, C18.P$1, C19.P$1, IC1.11 (AGND), IC1.78 (CV0), J1.1, J1.4, J1.7, J6.1, MOS1.P$1 (S1), R1.P$1
unnamed: MOS1.P$7 (D1), MOS1.P$8 (D1), R19.1
unnamed: IC1.71 (CV2), R4.P$2
unnamed: IC1.67 (CV3), R5.P$2
unnamed: IC1.75 (CV1), R3.P$2
unnamed: IC1.63 (CV4), R6.P$2
unnamed: IC1.59 (CV5), R7.P$2
unnamed: IC1.55 (CV6), R8.P$2
unnamed: IC1.51 (CV7), R9.P$2
unnamed: IC1.47 (CV8), R10.P$2
unnamed: IC1.43 (CV9), R11.P$2
unnamed: IC1.39 (CV10), R12.P$2
unnamed: IC1.35 (CV11), R13.P$2
unnamed: IC1.31 (CV12), R14.P$2
unnamed: IC1.27 (CV13), R15.P$2
unnamed: IC1.23 (CV14), R16.P$2
unnamed: IC1.19 (CV15), R17.P$2
unnamed: IC1.15 (CV16), R18.P$2
unnamed: MOS1.P$5 (D2), MOS1.P$6 (D2), R20.1
unnamed: MOS2.P$7 (D1), MOS2.P$8 (D1), R21.1
unnamed: MOS2.P$5 (D2), MOS2.P$6 (D2), R22.1
unnamed: MOS3.P$7 (D1), MOS3.P$8 (D1), R23.1
unnamed: MOS3.P$5 (D2), MOS3.P$6 (D2), R24.1
unnamed: MOS4.P$7 (D1), MOS4.P$8 (D1), R25.1
unnamed: MOS4.P$5 (D2), MOS4.P$6 (D2), R26.1
unnamed: MOS5.P$7 (D1), MOS5.P$8 (D1), R27.1
unnamed: MOS5.P$5 (D2), MOS5.P$6 (D2), R28.1
unnamed: MOS6.P$7 (D1), MOS6.P$8 (D1), R29.1
unnamed: MOS6.P$5 (D2), MOS6.P$6 (D2), R30.1
unnamed: MOS7.P$7 (D1), MOS7.P$8 (D1), R31.1
unnamed: MOS7.P$5 (D2), MOS7.P$6 (D2), R32.1
unnamed: MOS8.P$7 (D1), MOS8.P$8 (D1), R33.1
unnamed: MOS8.P$5 (D2), MOS8.P$6 (D2), R34.1
SAMPL: IC1.4 (SAMPL), J4.4
SCLK: IC1.1 (SCLK), J4.7
SDI: IC1.2 (SDI), J4.6
SDO: IC1.3 (SDO), J4.5
T1: IC1.9 (T1), J1.2
T2: IC1.8 (T2), J1.5
T3: IC1.7 (T3), J1.8
VP: C19.P$2, IC1.14 (VP), J6.2, R18.P$1, R34.2

Board: 2 copper layers, 69 parts (0 on the bottom side), 109 nets, no tracks yet.

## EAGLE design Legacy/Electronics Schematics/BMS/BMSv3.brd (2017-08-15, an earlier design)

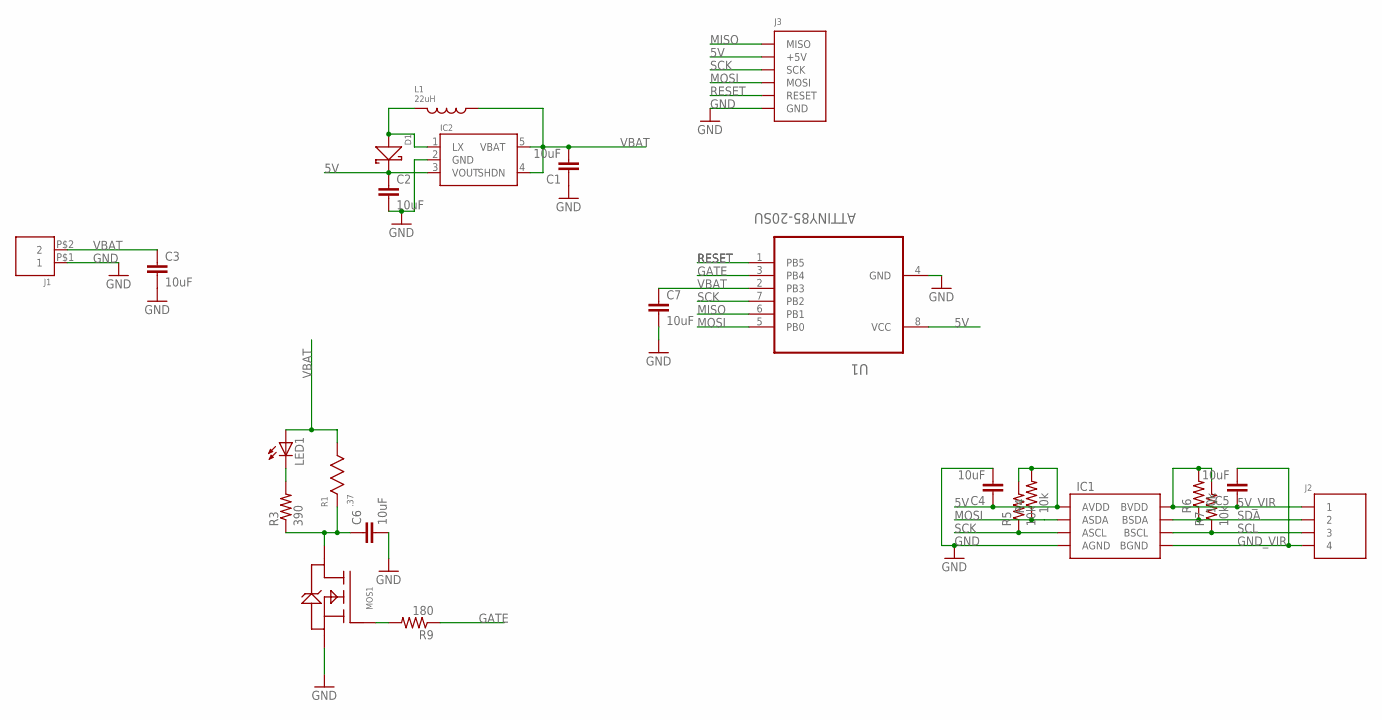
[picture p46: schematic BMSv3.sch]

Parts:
C1, C2, C3, C4, C5, C6, C7: 10uF; 0805-CAP
D1: DIODE_SCHOTTKYSOD-123; SOD-123
IC1: SI8600_DUALCHANNELISO; SOIC-8
IC2: SP6641; SOT-23
J1: CONNECTOR_2PIN; 2PIN_.1'
J2: CONNECTOR_4PIN; 4PIN_.1'
J3: ISPHEADER; 2X3PIN_.1'
L1: 22uH; 6X6MM_IND
LED1: LEDCHIPLED_0805; CHIPLED_0805
MOS1: MOS_N_LOGIC_PSMN7R0; LFPAK
R1: .37; TO-220-2
R3: 390; 0805
R4, R5, R6, R7: 10k; 0805
R9: 180; 0805
U1: ATTINY85-20SU; SOIC127P798X216-8N

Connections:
5V: C2.1, C4.1, D1.CATHODE, IC1.P$1 (AVDD), IC2.3 (VOUT), J3.P$2 (+5V), R4.2, R5.2, U1.8 (VCC)
5V_VIR: C5.1, IC1.P$8 (BVDD), J2.P$1 (1), R6.2, R7.2
GATE: R9.1, U1.3 (PB4)
GND: C1.1, C2.2, C3.2, C4.2, C6.2, C7.2, IC1.P$4 (AGND), IC2.2 (GND), J1.P$1 (1), J3.P$6 (GND), MOS1.P$1 (SOURCE), MOS1.P$2 (SOURCE), MOS1.P$3 (SOURCE), U1.4 (GND)
GND_VIR: C5.2, IC1.P$5 (BGND), J2.P$4 (4)
MISO: J3.P$1 (MISO), U1.6 (PB1)
MOSI: IC1.P$2 (ASDA), J3.P$4 (MOSI), R4.1, U1.5 (PB0)
unnamed: MOS1.P$4 (GATE), R9.2
unnamed: LED1.C, R3.2
unnamed: C6.1, MOS1.P$5 (DRAIN), R1.P$1, R3.1
unnamed: D1.ANODE, IC2.1 (LX), L1.P$1
RESET: J3.P$5 (RESET), U1.1 (PB5)
SCK: IC1.P$3 (ASCL), J3.P$3 (SCK), R5.1, U1.7 (PB2)
SCL: IC1.P$6 (BSCL), J2.P$3 (3), R7.1
SDA: IC1.P$7 (BSDA), J2.P$2 (2), R6.1
VBAT: C1.2, C3.1, C7.1, IC2.4 (SHDN), IC2.5 (VBAT), J1.P$2 (2), L1.P$2, LED1.A, R1.P$2, U1.2 (PB3)

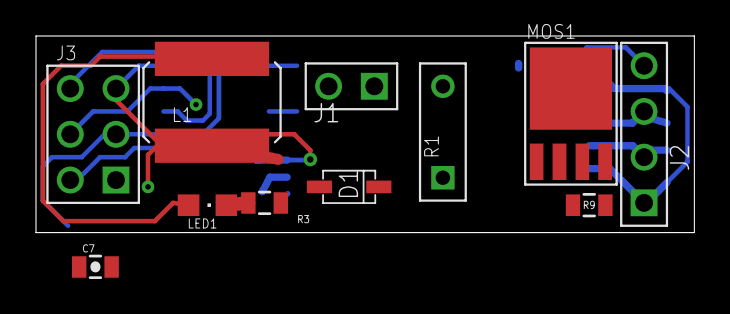
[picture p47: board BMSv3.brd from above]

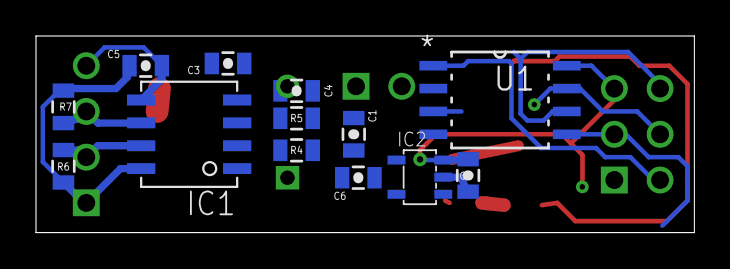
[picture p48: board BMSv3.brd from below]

Board: 2 copper layers, 36.6 x 10.9 mm, 24 parts (13 on the bottom side), 16 nets.

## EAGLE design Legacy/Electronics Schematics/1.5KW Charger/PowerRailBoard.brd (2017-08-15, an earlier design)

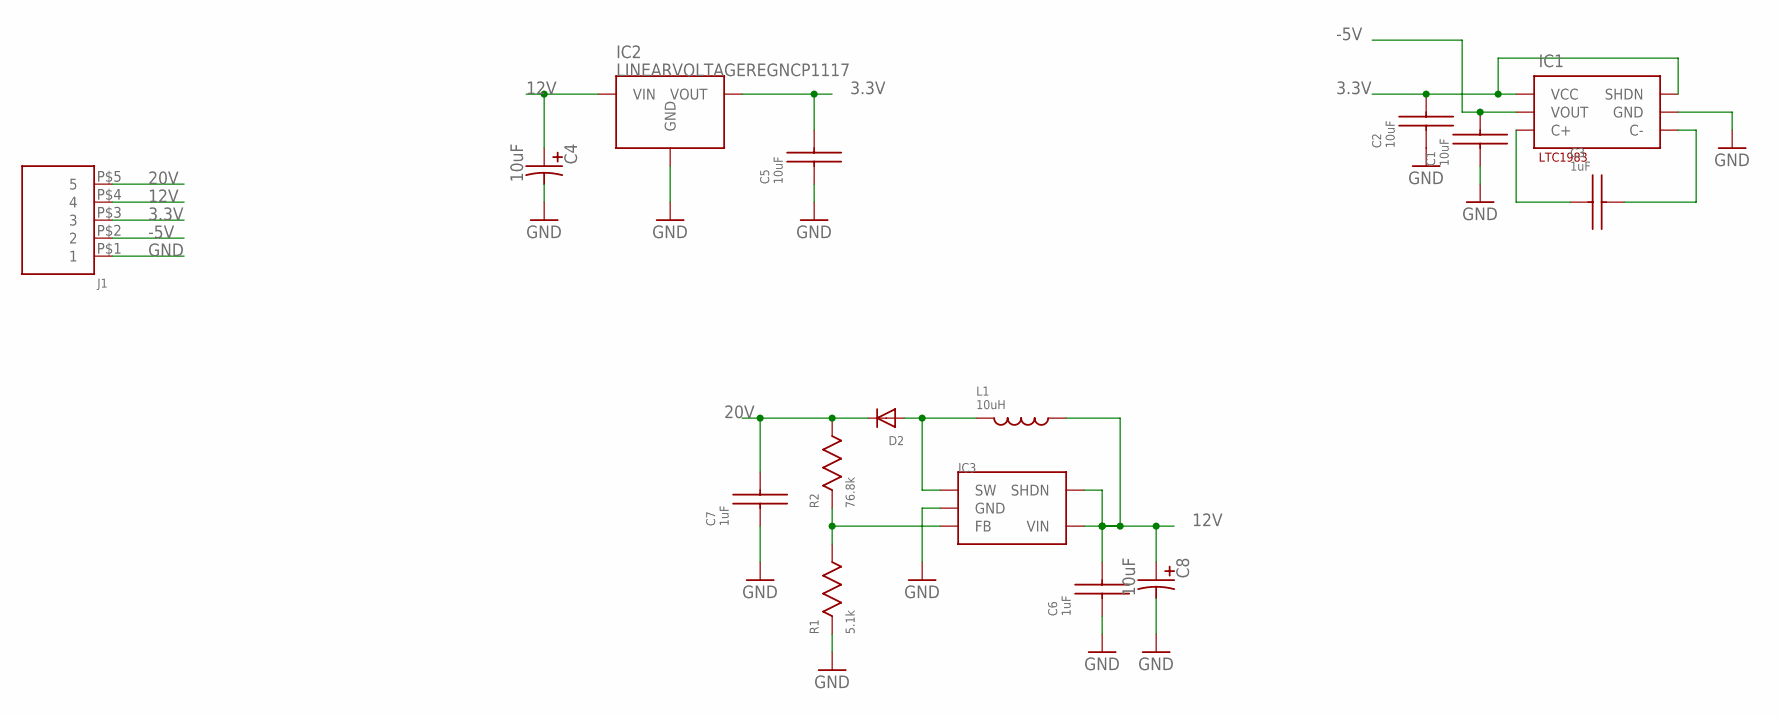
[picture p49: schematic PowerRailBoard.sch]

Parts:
C1, C2, C5: 10uF; 0805_(2012_METRIC)
C3, C6, C7: 1uF; 0805_(2012_METRIC)
C4, C8: 10uF; CAP_SSER_5MMX5MM
D2: DIODESOD-123; SOD-123
IC1: LTC1983; TSOT23-6
IC2: LINEARVOLTAGEREGNCP1117; DPAK
IC3: AP301; SOT-23
J1: CONNECTOR_5PIN; 5PIN_.1'
L1: 10uH; 0805_(2012_METRIC)
R1: 5.1k; 0805_(2012_METRIC)
R2: 76.8k; 0805_(2012_METRIC)

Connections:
3.3V: C2.P$1, C5.P$1, IC1.1 (VCC), IC1.6 (SHDN), IC2.2 (VOUT), J1.P$3 (3)
12V: C4.P (POSITIVE), C6.P$1, C8.P (POSITIVE), IC2.3 (VIN), IC3.4 (SHDN), IC3.5 (VIN), J1.P$4 (4), L1.P$2
20V: C7.P$1, D2.C, J1.P$5 (5), R2.P$1
-5V: C1.P$1, IC1.2 (VOUT), J1.P$2 (2)
GND: C1.P$2, C2.P$2, C4.N (NEGATIVE), C5.P$2, C6.P$2, C7.P$2, C8.N (NEGATIVE), IC1.5 (GND), IC2.1 (GND), IC3.2 (GND), J1.P$1 (1), R1.P$2
unnamed: C3.P$2, IC1.3 (C+)
unnamed: C3.P$1, IC1.4 (C-)
unnamed: D2.A, IC3.1 (SW), L1.P$1
unnamed: IC3.3 (FB), R1.P$1, R2.P$2

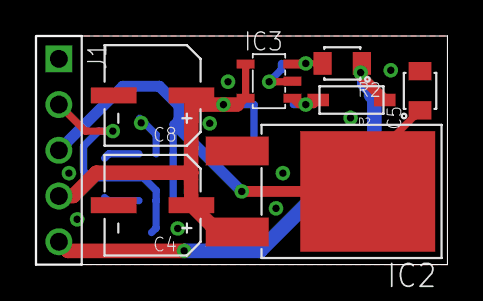
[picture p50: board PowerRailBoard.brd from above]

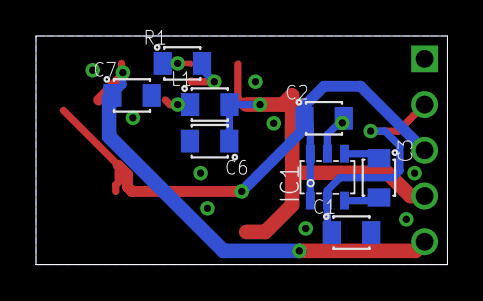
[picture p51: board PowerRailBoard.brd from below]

Board: 2 copper layers, 22.9 x 12.7 mm, 16 parts (8 on the bottom side), 9 nets.

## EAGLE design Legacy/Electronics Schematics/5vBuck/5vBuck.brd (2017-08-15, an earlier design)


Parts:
C1: 10uF; NIPPON_F80
C2, C3: 0.1uF; 0805-CAP
C4, C5: 22uF; 0805-CAP
C6: 1uF; 0805-CAP
D1: DIODE_SCHOTTKYSOD-123; SOD-123
IC1: M5033; SOIC-8
J1: CONNECTOR_4PIN; 4PIN_.1'
L1: 220uH; 6X6MM_IND
R1: 670k; 0805
R2: 220k; 0805
U1: BSS138P; SOT95P230X110-3N

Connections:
GND: C1.-, C3.2, C4.2, C5.2, C6.2, D1.ANODE, IC1.P$3 (SGND), IC1.P$6 (GND), J1.P$2 (2), R2.2, U1.2 (S)
IO: IC1.P$5 (ON/OFF), R1.2, R2.1, U1.3 (D)
unnamed: C2.2, D1.CATHODE, IC1.P$8 (LX), L1.P$1
unnamed: C2.1, IC1.P$1 (BST)
unnamed: C3.1, IC1.P$2 (VD)
SHDN: J1.P$4 (4), U1.1 (G)
VIN: C1.+, IC1.P$7 (VIN), J1.P$1 (1), R1.1
VOUT: C4.1, C5.1, C6.1, IC1.P$4 (FB), J1.P$3 (3), L1.P$2

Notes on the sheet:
UVLO = (1+r1/r2)*1.85v



Board: 2 copper layers, 10.2 x 17.3 mm, 13 parts (10 on the bottom side), 8 nets.

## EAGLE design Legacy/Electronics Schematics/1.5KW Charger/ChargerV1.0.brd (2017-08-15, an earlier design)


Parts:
B1: B25A-
B2, B3: MB1S; SOIC-4
C1, C2, C7, C8, C15, C16, C17, C18: .47uF; C1206
C3, C4: .1uF; C1206
C5, C19: CPOL-USE2.5-7; E2,5-7
C6, C20: .1uF; 0805-CAP
C9, C13, C14: 1uF; 0805-CAP
C10: 10uF; 0805-CAP
C11, C12: 0.1uF; 0805-CAP
C21: 2200uF; EB30D
C22, C23, C24: CPOL-USE10-30; EB30D
D1, D2: DIODESMA; SMADIODE
D5: 5.1V; SOD-323
F1: FUSE; FUSE_HOLDER
IC1: SI8600_DUALCHANNELISO; SOIC-8
IC2, IC3: FAN7190; SOIC-8
J1: ISPHEADER; 2X3PIN_.1'
L1: 5:1; TRANSFORMER_TOR_CUSTOM
L2: 24:1:1; TRANSFORMER_CUSTOM1
LED1, LED2, LED3: LEDCHIPLED_0805; CHIPLED_0805
Q1, Q2, Q3, Q4: FDA69N25; TO247BV
R1, R2, R3: 1k; 0805
R4, R5, R6, R7: 10k; 0805
U1: ATMEGA328P-AU; QFP80P900X900X120-32N
X1: 22-23-2041
X2: 6ESRM-P

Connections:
5V: B3.+, C6.1, C9.1, C10.1, C11.1, C12.2, C13.2, C14.1, C19.+, D5.C, IC1.P$1 (AVDD), J1.P$2 (+5V), R4.2, R5.2, U1.4 (VCC_2), U1.6 (VCC), U1.18 (AVCC)
5V_SEC: B2.+, C5.+, C20.1, IC1.P$8 (BVDD), R6.2, R7.2, X1.1
ACRECT: B1.+1 (+), C21.+, C22.+, C23.+, C24.+, Q1.D, Q3.D
GND: B1.-1 (-), B3.-, C6.2, C9.2, C10.2, C11.2, C12.1, C13.1, C14.2, C19.-, C21.-, C22.-, C23.-, C24.-, D1.A, D2.A, D5.A, IC1.P$4 (AGND), IC2.P$3 (COM), IC2.P$5 (VDD), IC3.P$3 (COM), IC3.P$5 (VDD), J1.P$6 (GND), LED1.C, LED2.C, LED3.C, Q2.S, Q4.S, U1.3 (GND_2), U1.5 (GND_3), U1.21 (GND), X2.2 (SH)
GND_SEC: B2.-, C5.-, C20.2, IC1.P$5 (BGND), X1.4
HO1: IC2.P$7 (HO), Q1.G
HO2: IC3.P$7 (HO), Q3.G
HSO: C1.2, C3.2, C7.1, C8.1, C15.1, C16.1, C17.1, C18.1, IC2.P$6 (VS), Q3.S, Q4.D
HS_SEC: L1.P$4
IN_HO1: IC2.P$2 (LIN), IC3.P$1 (HIN), U1.9 (PD5)
IN_HO2: IC2.P$1 (HIN), IC3.P$2 (LIN), U1.10 (PD6)
LEDG: R1.1, U1.30 (PD0)
LEDR: R3.1, U1.32 (PD2)
LEDY: R2.1, U1.31 (PD1)
LO1: IC2.P$4 (LO), Q2.G
LO2: IC3.P$4 (LO), Q4.G
LSO: C2.2, C4.2, IC3.P$6 (VS), L1.P$2, Q1.S, Q2.D
LS_SEC: L1.P$3
MISO: J1.P$1 (MISO), U1.16 (PB4)
MOSI: J1.P$4 (MOSI), U1.15 (PB3)
unnamed: F1.P$1, F1.P$2, L2.IN2, X2.3 (AC2)
unnamed: B1.AC1- (AC1), F1.P$3, F1.P$4
unnamed: B1.AC2- (AC2), L2.IN1, X2.1 (AC1)
unnamed: B3.~1 (AC1), L2.OUT11
unnamed: B3.~2 (AC2), L2.OUT12
unnamed: B2.~1 (AC1), L2.OUT21
unnamed: B2.~2 (AC2), L2.OUT22
unnamed: LED2.A, R1.2
unnamed: LED1.A, R2.2
unnamed: C1.1, C3.1, D1.C, IC2.P$8 (VB)
unnamed: C2.1, C4.1, D2.C, IC3.P$8 (VB)
unnamed: LED3.A, R3.2
unnamed: C7.2, C8.2, C15.2, C16.2, C17.2, C18.2, L1.P$1
RESET: J1.P$5 (RESET), U1.29 (PC6)
SCK: J1.P$3 (SCK), U1.17 (PB5)
SCL: IC1.P$3 (ASCL), R5.1, U1.28 (PC5)
SCL_SEC: IC1.P$6 (BSCL), R7.1, X1.3
SDA: IC1.P$2 (ASDA), R4.1, U1.27 (PC4)
SDA_SEC: IC1.P$7 (BSDA), R6.1, X1.2

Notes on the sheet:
2.82uF Total
Highside
Lowside
Primary Side
Secondary Side
EDIT CAPS need higher passing current
fuck it use ldo



Board: 2 copper layers, 162.5 x 106.3 mm, 54 parts (23 on the bottom side), 37 nets.

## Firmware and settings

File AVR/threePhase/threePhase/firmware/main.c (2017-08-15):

#include <avr/io.h>
#include <util/delay.h>

#define phaseAL PB0
#define phaseBL PB1
#define phaseCL PB2

#define phaseAH PB3
#define phaseBH PB4
#define phaseCH PB5


void timer0_init(int prescaler)
{
    if(prescaler==1)                    //clk/1
    {
        TCCR0 |= (1 << CS00);
    }
    if(prescaler==8)                    //clk/8
    {
        TCCR0 |= (1 << CS01);
    }
    if(prescaler==64)                    //clk/64
    {
        TCCR0 |= (1 << CS00)|(1<<CS01);
    }
    if(prescaler==256)                    //clk/256
    {
        TCCR0 |= (1<<CS02);
    }
    if(prescaler==1024)                    //clk/1024
    {
        TCCR0 |= (1 << CS00)|(1<<CS02);
    }
}

void timer1_init(int prescaler)
{
    if(prescaler==1)                    //clk/1
    {
        TCCR1B |= (1 << CS10);
    }
    if(prescaler==8)                    //clk/8
    {
        TCCR1B |= (1 << CS11);
    }
    if(prescaler==64)                    //clk/64
    {
        TCCR1B |= (1 << CS10)|(1<<CS11);
    }
    if(prescaler==256)                    //clk/256
    {
        TCCR1B |= (1<<CS12);
    }
    if(prescaler==1024)                    //clk/1024
    {
        TCCR1B |= (1 << CS10)|(1<<CS12);
    }
}

void timer2_init(int prescaler)
{
    if(prescaler==1)                    //clk/1
    {
        TCCR2 |= (1 << CS20);
    }
    if(prescaler==8)                    //clk/8
    {
        TCCR2 |= (1 << CS21);
    }
    if(prescaler==32)                    //clk/32
    {
        TCCR2 |= (1 << CS21)|(1<<CS20);
    }
    if(prescaler==64)                    //clk/64
    {
        TCCR2 |= (1 << CS22);
    }
    if(prescaler==128)                    //clk/128
    {
        TCCR2 |= (1<<CS22)|(1<<CS20);
    }
    if(prescaler==256)                    //clk/256
    {
        TCCR2 |= (1 << CS22)|(1<<CS21);
    }
    if(prescaler==1024)                    //clk/1024
    {
        TCCR2 |= (1 << CS22)|(1<<CS21)|(1<<CS20);
    }
}

void phaseFire(int phase, int condition)
{
    if(phase == 1) //PhaseAH
    {
        if(condition==1)
        {
            PORTD |= (1<<phaseAH);
        }
        else
        {
            PORTD &= ~(1<<phaseAH);
        }
    }
    if(phase == 2) //PhaseBH
    {
        if(condition==1)
        {
            PORTD |= (1<<phaseBH);
        }
        else
        {
            PORTD &= ~(1<<phaseBH);
        }
    }
    if(phase == 3) //PhaseCH
    {
        if(condition==1)
        {
            PORTD |= (1<<phaseCH);
        }
        else
        {
            PORTD &= ~(1<<phaseCH);
        }
    }
    if(phase == 4) //PhaseAL
    {
        if(condition==1)
        {
            PORTD |= (1<<phaseAL);
        }
        else
        {
            PORTD &= ~(1<<phaseAL);
        }
    }
    if(phase == 5) //PhaseBL
    {
        if(condition==1)
        {
            PORTD |= (1<<phaseBL);
        }
        else
        {
            PORTD &= ~(1<<phaseBL);
        }
    }
    if(phase == 6) //PhaseCL
    {
        if(condition==1)
        {
            PORTD |= (1<<phaseCL);
        }
        else
        {
            PORTD &= ~(1<<phaseCL);
        }
    }
}

void cycle(int phase, int duty, int duration)
{
// (A/B/C,0-255,(ms))
//pass which phase, duration, and the duty cycle at which to perform a single cycle
    if(phase==1)//PhaseAH
    {
        
        phaseFire(2,0); //Set PhaseBH Low
        phaseFire(3,0); //Set PhaseCH Low
        phaseFire(5,1); //Set PhaseBL High
        phaseFire(6,1); //Set PhaseCL High
        
        phaseFire(4,0); //Set PhaseAL Low
        
        timer0_init(1024);//timer 0 measures duration of entire cycle
        timer2_init(1);//timer 1 measures duty cycles
        TCNT0 = 0;
        TCNT2 = 0;

        while(TCNT0<=duration)
        {
            if(TCNT2<duty)
            {
                phaseFire(1,1);
            }
            else
            {
                phaseFire(1,0);
            }
        }
        phaseFire(1,0);
        return;
    }
    if(phase==2)//PhaseBH
    {
        
        phaseFire(1,0); //Set PhaseAH Low
        phaseFire(3,0); //Set PhaseCH Low
        phaseFire(4,1); //Set PhaseAL High
        phaseFire(6,1); //Set PhaseCL High
        
        phaseFire(5,0); //Set PhaseBL Low
        
        timer0_init(1024);//timer 0 measures duration of entire cycle
        timer2_init(1);//timer 1 measures duty cycles
        TCNT0 = 0;
        TCNT2 = 0;
        while(TCNT0<=duration)
        {
            if(TCNT2<duty)
            {
                phaseFire(2,1);
            }
            else
            {
                phaseFire(2,0);
            }
        }
        phaseFire(2,0);
        return;
    }
    if(phase==3)//PhaseCH
    {
        
        phaseFire(1,0); //Set PhaseAH Low
        phaseFire(2,0); //Set PhaseBH Low
        phaseFire(4,1); //Set PhaseAL High
        phaseFire(5,1); //Set PhaseBL High
        
        phaseFire(6,0); //Set PhaseCL Low
       
        timer0_init(1024);//timer 0 measures duration of entire cycle
        timer2_init(1);//timer 1 measures duty cycles
        TCNT0 = 0;
        TCNT2 = 0;
        while(TCNT0<=duration)
        {
            if(TCNT2<duty)
            {
                phaseFire(3,1);
            }
            else
            {
                phaseFire(3,0);
            }
            
        }
        phaseFire(3,0);
        return;
    }
}

void fade(int duty, int duration)
{
    for (duty = 1; duty < 255; ++duty)
    {
        phaseFire(2,0);
        phaseFire(3,0);
        cycle(1,duty,duration);
        phaseFire(1,0);
        
        phaseFire(1,0);
        phaseFire(3,0);
        cycle(2,duty,duration);
        phaseFire(2,0);
        
        phaseFire(1,0);
        phaseFire(2,0);
        cycle(3,duty,duration);
        phaseFire(3,0);
    }
    for (duty = 255; duty > 1; --duty)
    {
        
        phaseFire(2,0);
        phaseFire(3,0);
        cycle(1,duty,duration);
        phaseFire(1,0);
        
        phaseFire(1,0);
        phaseFire(3,0);
        cycle(2,duty,duration);
        phaseFire(2,0);
        
        phaseFire(1,0);
        phaseFire(2,0);
        cycle(3,duty,duration);
        phaseFire(3,0);
    }
}

void degreeFire(int degree)
{
    if(degree <= 60)
        //A Increasing
        //B Zero
        //C Max
    {
        phaseFire(2,0);
        phaseFire(3,1);
        
    }
    
    if(degree <= 120)
        //A Max
        //B Zero
        //C Decreasing
    {
        
    }
    
    if(degree <= 180)
        //A Max
        //B Increasing
        //C Zero
    {
        
    }
    
    if(degree <= 240)
        //A Decreasing
        //B Max
        //C Zero
    {
        
    }
    
    if(degree <= 300)
        //A Zero
        //B Max
        //C Increasing
    {
        
    }
    
    if(degree <= 360)
        //A Zero
        //B Decreasing
        //C Max
    {
        
    }
}

int main(void)
{
    DDRD |= (1 << phaseAH);
    DDRD |= (1 << phaseBH);
    DDRD |= (1 << phaseCH);
    DDRD |= (1 << phaseAL);
    DDRD |= (1 << phaseBL);
    DDRD |= (1 << phaseCL);
    int duty = 40;
    int duration = 50;                    // make sure duration can never be larger than 2
    int i;
    int ramp = 5;
    
    while(1)
    {
        for(i=10;i<20;i++)
        {
        cycle(1,i,ramp);
        }
        cycle(1,duty,duration);
        for(i=20;i>10;i--)
        {
        cycle(1,i,ramp);
        }
        
        
        for(i=10;i<20;i++)
        {
            cycle(2,i,ramp);
        }
        cycle(2,duty,duration);
        for(i=20;i>10;i--)
        {
            cycle(2,i,ramp);
        }
        
        
        for(i=10;i<20;i++)
        {
            cycle(3,i,ramp);
        }
        cycle(3,duty,duration);
        for(i=20;i>10;i--)
        {
            cycle(3,i,ramp);
        }
       // cycle(2,duty,duration);
        //cycle(3,duty,duration);
        /*
        for(i = 240; i>60;i--)
        {
        cycle(1,duty,i);
        cycle(2,duty,i+1);
        cycle(3,duty,i+2);
        }
        for(i = 60; i<240 ;i++)
        {
            cycle(1,duty,i);
            cycle(2,duty,i+1);
            cycle(3,duty,i+2);
        }
         */

    }
    return 0;
}

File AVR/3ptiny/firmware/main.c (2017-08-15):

/*
#include <avr/io.h>
#include <util/delay.h>
#define Red PB2

void setup()
{
    DDRB |= (1 << Red);
}

int main()
{
    setup();
    
    while(1)
    {
        
        _delay_ms(50);	//delay for 50 ms
        PORTB ^= (1<<Red);    //Toggle Red
    }
    return 0;
}

*/

#include <avr/io.h>
#include <util/delay.h>

#define Blue PB0
#define Green PB1
#define Red PB2

void timer0_init(int prescaler)
{
    if(prescaler==1)                    //clk/1
    {
        TCCR0B |= (1 << CS00);
    }
    if(prescaler==8)                    //clk/8
    {
        TCCR0B |= (1 << CS01);
    }
    if(prescaler==64)                    //clk/64
    {
        TCCR0B |= (1 << CS00)|(1<<CS01);
    }
    if(prescaler==256)                    //clk/256
    {
        TCCR0B |= (1<<CS02);
    }
    if(prescaler==1024)                    //clk/1024
    {
        TCCR0B |= (1 << CS00)|(1<<CS02);
    }
}


void phaseFire(int degree)
{
    if(degree<=60)
    {
        
        int duty = (degree*255)/60;
        PORTB |= (1<<Red);      //Turn Red on
        PORTB |= (1<<Blue);    //Turn Blue on
        PORTB &= ~(1<<Green);    //Turn Green off
        TCNT0=0;
        while(TCNT0<255)
        {
            if(TCNT0>duty)
            {
                PORTB &= ~(1<<Red);
            }
        }
    return;
    }
    if(degree<=120)
    {
        
        int duty = ((120-degree)*255)/60;
        PORTB |= (1<<Red);      //Turn Red on
        PORTB |= (1<<Blue);    //Turn Blue on
        PORTB &= ~(1<<Green);    //Turn Green off
        TCNT0=0;
        while(TCNT0<255) 
        {
            if(TCNT0>duty)
            {
                PORTB &= ~(1<<Blue);
            }
        }
        return;
    }
    if(degree<=180)
    {
        
        int duty = ((degree-120)*255)/60;
        PORTB |= (1<<Red);      //Turn Red on
        PORTB |= (1<<Green);    //Turn Green on
        PORTB &= ~(1<<Blue);    //Turn Blue off
        TCNT0=0;
        while(TCNT0<255)
        {
            if(TCNT0>duty)
            {
                PORTB &= ~(1<<Green);
            }
        }
        return;
    }
    if(degree<=240)
    {
        
        int duty = ((240-degree)*255)/60;
        PORTB |= (1<<Red);      //Turn Red on
        PORTB |= (1<<Green);    //Turn Green on
        PORTB &= ~(1<<Blue);    //Turn Blue off
        TCNT0=0;
        while(TCNT0<255)
        {
            if(TCNT0>duty)
            {
                PORTB &= ~(1<<Red);
            }
        }
        return;
    }
    if(degree<=300)
    {
        
        int duty = ((degree-240)*255)/60;
        PORTB &= ~(1<<Red);      //Turn Red off
        PORTB |= (1<<Green);    //Turn Green on
        PORTB |= (1<<Blue);    //Turn Blue on
        TCNT0=0;
        while(TCNT0<255)
        {
            if(TCNT0>duty)
            {
                PORTB &= ~(1<<Blue);
            }
        }
        return;
    }
    if(degree<=360)
    {
        
        int duty = ((360-degree)*255)/60;
        PORTB &= ~(1<<Red);      //Turn Red off
        PORTB |= (1<<Green);    //Turn Green on
        PORTB |= (1<<Blue);    //Turn Blue on
        TCNT0=0;
        while(TCNT0<255)
        {
            if(TCNT0>duty)
            {
                PORTB &= ~(1<<Green);
            }
        }
        return;
    }
    
    return;
}


int main(void)
{
    
    DDRB |= (1 << Red);
    DDRB |= (1 << Green);
    DDRB |= (1 << Blue);
    timer0_init(64);
    int degree = 0;
    while(1)
    {
        for(degree=0; degree<360; degree++)
        {
            phaseFire(degree);
        }
        
    }
    return 0;
}

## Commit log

2017-08-15 added MarkII project
    [10cal_hanger.SLDPRT, 10cal_hangerEDIT.SLDPRT, 26650B1x6.SLDPRT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]
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2017-08-16 deck symmetry attained, tubular battery holders made
    [50cal_baseplateEDIT.SLDPRT, 608-bearing.SLDPRT, 90967A120_STAINLESS STEEL EXTERNAL RETAINING RING.SLDPRT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]
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2017-08-17 tubular batterypack expanded to hold 64 cells, spring compression fitting
    [18guage3_4incopperdisk.SLDPRT, 28mmID carbonfiber Tube_contouredV2.SLDPRT, 50cal_baseplateEDIT.SLDPRT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]
2017-08-17 routed each cell, no issues in tubular battery pack assembly
    [18guage3_4incopperdisk.SLDPRT, 1_125inID carbonfiber Tube_contouredV1.SLDPRT, 28mmID carbonfiber Tube_contouredV2.SLDPRT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]
2017-08-17 Final Assembly V8 Created, includes powerpack subassembly
    [18guage3_4incopperdisk.SLDPRT, 1_125inID carbonfiber Tube_contouredV1.SLDPRT, 28mmID carbonfiber Tube_contouredV2.SLDPRT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]
2017-08-17 pack connectors are now an assembly
    [18guage3_4incopperdisk.SLDPRT, 1_125inID carbonfiber Tube_contouredV1.SLDPRT, 50cal_baseplateEDIT.SLDPRT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]
2017-08-18 Deck Redesign 9th itiration of the final assembly
    [18guage3_4incopperdisk.SLDPRT, 1_125inID carbonfiber Tube_contouredV1.SLDPRT, 50cal_baseplateEDIT.SLDPRT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]
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2017-08-18 fixed minor assembly errors in assembly
    [18guage3_4incopperdisk.SLDPRT, 1_125inID carbonfiber Tube_contouredV1.SLDPRT, 91251A146_BLACK-OXIDE ALLOY STEEL SOCKET HEAD CAP SCREW.SLDPRT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]
2017-08-18 photos added, ReadMe updated
    [BMS.brd, BMS.sch, BMSChargerV1.sch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]
2017-08-20 Organized the mess a bit
    [18guage3_4incopperdisk.SLDPRT, 1_125inID carbonfiber Tube_contouredV1.SLDPRT, 26650B1x6.SLDPRT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]
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2017-08-22 Terrain collsision test round 1
    [18guage3_4incopperdisk.SLDPRT, 1_125inID carbonfiber Tube_contouredV1.SLDPRT, 50cal_baseplateEDIT.SLDPRT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]
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2017-08-28 EndCap assmble for Tubular Packs
    [DeckAndPackV3.SLDASM, EndCapAssem.SLDASM, TubularPackV3.SLDASM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]
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2017-08-30 fixed tub pack assembly errors and started press
    [18guage3_4incopperdisk.SLDPRT, 1_125inID carbonfiber Tube_contouredV1.SLDPRT, 9657K314_STEEL COMPRESSION SPRING.SLDPRT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]
2017-08-30 added tubular pack endcap pcb
    [18guage3_4incopperdisk.SLDPRT, 1_125inID carbonfiber Tube_contouredV1.SLDPRT, 9657K314_STEEL COMPRESSION SPRING.SLDPRT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]
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2017-09-03 BOM, Spacer, Bumper draft
    [Assem2.SLDASM, DeckAndPackV3.SLDASM, DeckMoldBOM.xlsx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]
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2017-09-08 Grindbridge adjust + BOM + hardware inclusion beggining
    [18guage3_4incopperdisk.SLDPRT, 1_125inID carbonfiber Tube_contouredV1.SLDPRT, 91251A157_BLACK-OXIDE ALLOY STEEL SOCKET HEAD CAP SCREW.SLDPRT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]
2017-09-10 fasteners folder, BOM for battery pack
    [18guage3_4incopperdisk.SLDPRT, 1_125inID 1_25OD Acrylic Tube_contoured.SLDPRT, 1_125inID carbonfiber Tube_contouredV1.SLDPRT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]
2017-09-10 Compiled Bat Holder BOM
    [18guage3_4incopperdiskV4T&PAcryl.SLDPRT, 1_125inID 1_25OD Acrylic Tube_contoured.SLDPRT, 1_125inID carbonfiber Tube_contouredV1V4T&PAcryl.SLDPRT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]
2017-09-16 CNC cam file start, BOM update
    [18guage3_4incopperdisk.SLDPRT, 1_125inID 1_25OD Acrylic Tube_contoured.SLDPRT, 20guage3_4incopperdisk.SLDPRT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]
2017-09-20 grind rails and updated bat holder assembly
    [18guage3_4incopperdisk.SLDPRT, 1_125inID 1_25OD Acrylic Tube_contoured.SLDPRT, 20guage3_4incopperdisk.SLDPRT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]
2017-09-22 grind rail CNC CAM work
    [18guage3_4incopperdisk.SLDPRT, 1_125inID 1_25OD Acrylic Tube_contoured.SLDPRT, 20guage3_4incopperdisk.SLDPRT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]
2017-10-01 Renders for project log
    [GrindRailV2_W_ScrewsV4T&PAcryl.SLDASM, Long bridge grind railV2V4T&PAcryl.SLDPRT, Turnigy6374.SLDASM]
2017-10-01 added EV sensor module
    [0204 - Capacitor Brown.SLDPRT, 0204 - Capacitor.SLDPRT, 0204- Resistor.SLDPRT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]
2017-10-01 EV module full assembly
    [Full Electronics Assembly.SLDASM]
2017-10-02 EV module final assembly update
    [Full Electronics Assembly.SLDASM]
2017-10-03 Mold update and redo
    [18guage3_4incopperdisk.SLDPRT, 1_125inID 1_25OD Acrylic Tube_contoured.SLDPRT, 20guage3_4incopperdisk.SLDPRT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]
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2017-10-04 battery spacer and contact re-designed
    [1_125inID 1_25OD Acrylic Tube_contoured.SLDPRT, ANR26650 Battery.SLDPRT, Assem1.SLDASM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]
2017-10-16 Battery connector updated, GPS Module enclosure made
    [1_125inID 1_25OD Acrylic Tube_contoured.SLDPRT, 1_125inID 1_25OD Acrylic Tube_contouredV2.SLDPRT, 92949A832_18-8 SS BUTTON-HEAD SOCKET CAP SCREW.SLDPRT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]
2017-10-17 Exploded view, Project Porfolio
    [18guage3_4incopperdisk.SLDPRT, 1_125inID 1_25OD Acrylic Tube_contoured.SLDPRT, 50cal_baseplateEDIT.SLDPRT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]
2017-11-07 touchups, mainly working in hardware atm
    [1_125inID 1_25OD Acrylic Tube_contoured.SLDPRT, ANR26650 Battery.SLDPRT, Assem2.SLDASM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]
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2017-11-24 Electronics start, GPS code
    [BatterySpacer1.brd, BatterySpacer1.sch, Data1.csv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]
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2018-01-28 BMS MAX14921 Board Rev 1
    [BMSMAX14921Based.brd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]
2018-01-31 connector PCBs and such
    [18guage3_4incopperdisk.SLDPRT, 1_125inID 1_25OD Acrylic Tube_contoured.SLDPRT, 50cal_baseplateEDIT.SLDPRT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]
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2018-02-01 dual pcb layer connector
    [1_125inID 1_25OD Acrylic Tube_contoured.SLDPRT, 50cal_baseplateEDIT.SLDPRT, 608-bearing.SLDPRT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]
2018-02-04 cleaned up files, created legacy folders
    [18guage3_4incopperdisk.SLDPRT, 18guage3_4incopperdiskV4T&PAcryl.SLDPRT, 1_125inID 1_25OD Acrylic Tube_contoured.SLDPRT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]
2018-02-05 redesigned PCBEndCap to include GND and VCC
    [1692K110_TYPE 302 SS CONICAL COMPRESSION SPRING.SLDPRT, 50cal_baseplateEDIT.SLDPRT, 608-bearing.SLDPRT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]
2018-02-05 front pcbconnector redesigned
    [1692K110_TYPE 302 SS CONICAL COMPRESSION SPRING.SLDPRT, 1692K530_TYPE 302 SS CONICAL COMPRESSION SPRING.SLDPRT, 90114A608_BRASS FILLISTER HEAD SLOTTED MACHINE 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]
2018-02-06 vesc and backend connectors adjusted
    [1692K530_TYPE 302 SS CONICAL COMPRESSION SPRING.SLDPRT, 50cal_baseplateEDIT.SLDPRT, 608-bearing.SLDPRT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]
2018-02-11 pcb spacer and breakoutoard over
    [50cal_baseplateEDIT.SLDPRT, 608-bearing.SLDPRT, 90114A608_BRASS FILLISTER HEAD SLOTTED MACHINE SCREW.SLDPRT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]
2018-02-26 updated Max14921 Breakout Board
    [BMSMAX14921Based.brd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]

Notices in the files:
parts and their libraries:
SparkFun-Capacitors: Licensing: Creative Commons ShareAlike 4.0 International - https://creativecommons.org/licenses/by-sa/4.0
